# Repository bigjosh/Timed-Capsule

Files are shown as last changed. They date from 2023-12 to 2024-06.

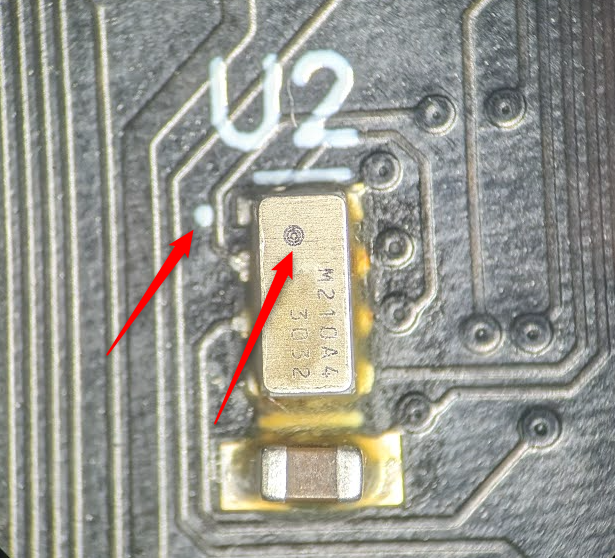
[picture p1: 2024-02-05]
hardware/assembly-package/Orientation U2.png

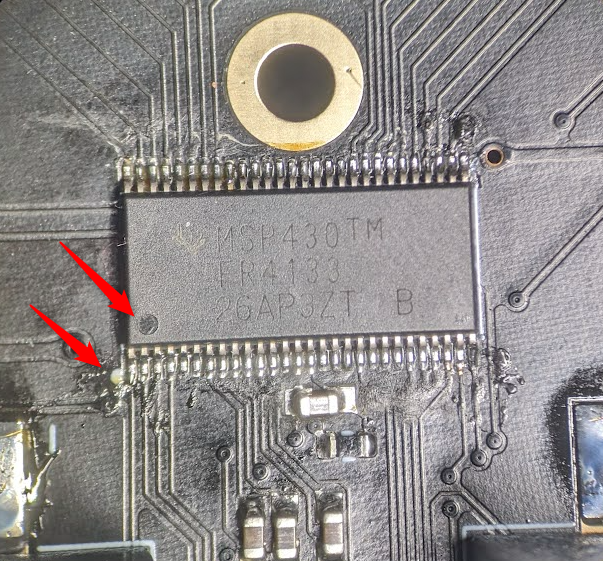
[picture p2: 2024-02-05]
hardware/assembly-package/Orientation U1.png

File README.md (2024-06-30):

# Timed Capsule

PCB and firmware for the CW&T Timed Capsule project.



The Timed Capsule is a commitment device. You put something in the capsule and set the timer for between 1 hour and 100 years and you will not be able to (nondestructively) get the thing for that long. 



## Design goals:

* Run for decades on 2xAA batteries.
* Stay accurate to to within ±2ppm over the lifetime.
* Have enough power at the end of 50 years in storage to still be able to decisively open the locking mechanisim. 
* Replaceable batteries

## Critical parts:

* MSP430FR4133 processor for LCD driving and supervision
* RV3032-C7 RTC for precision timekeeping
* 7-digit, dynamic LCD glass 
* 4x Energizer Ultimate Lithium AA batteries
* Solenoids which pull decicively at 6V
* Optional TPS7A0230 3V regulator for generating LCD bias voltage

## Method of Operation

### Set timer

Use the `MOVE` button to change cursor posision on the LCD, use the `CHANGE` button to change the current position. 

The rightmost position is the units and can be...

| Value | Units | 
| - | - |
| `H` | Hours |
| `d` | Days |
| `y` | Years | 

Note that a [year is 365.2422 days](https://pumas.nasa.gov/sites/default/files/examples/04_21_97_1.pdf). 

### Lock 

1. Turn the locking handle on the top clockwise 1/4 turn until it stops.
2. Release the handle and let it return to the resting position.

### Wait

Durring the countdown, the LCD  will rotate though...

1. Days remaining as 'xxxxxd`.
2. Hours, minutes, and seconds until the current day is done as `HHMMSS`.

... stopping on each screen for 1 second. 

If there is less than 1 day remaing until unlock, then the `HHMMMSS` display will show continuously. 

### Unlock

At the appointed hour, the locking mechanisim will automatically retract with a satisfying thud. You should then be able to remove the cap.

Note that the mechanisim will not be able to release unless the handle is in the resting position (turned all the way counter clockwise). If you accedentially turn the handle clockwise when the mechanisim is unlocking, then it will stay locked.
Since the timer automatically resets to 1 hour after each unlock attempt, you can turn the handle counter clockwise and then clockwise again to restart the countdown and - as long as you let the handle return to the resting position- it will unlock then.

## Interesting twists

### Solenoids

It is hard to find common solenoids that definitively actuate at voltages/currents available with our AA batteries, so we picked the solenoids carefully and use an extra pair AA batteries soley for a voltage boost at the moment we pull them. You might suggest using either a boost inductor-based boost circuit or a capacitor-based charge pump to avoid ths, but it would require some very big parts to store enough energy to be useful here (we can not use electrolitic caps since they will likely fail over the decades). It is hard to compete with the density of chemical energy! You might also suggest using a motor and gears to do the actuation (this is how most battery powered door locks do it), but it is hard to imagine gears that stay reliable after sitting still for 50 years. 

### Oscilator

We are using the MSP430's Very Low Power Oscilator (VLO) to drive the LCD since it is actually lower power than the 32Khz XTAL. It is also slower, so more power savings. The internal VLO also empreically uses less total power than using the RV3032 clkout to drive the MSP430's LCD clock, which is supprising. 

### MSP430 LPMx.5 modes

We do NOT use the MSP430's "LPMx.5" extra low power modes since they end up using more power than the "LPM4" mode that we are using. This is becuase it takes 250us to wake from the "x.5" modes and durring this time, the MCU pulls about 200uA. Since we wake every second, this is just not worth it. If we only woke every, say, 15 seconds then we could likely save ~0.3uA by using the "x.5" modes.

### LCD software optimications

To make LCD updates as power efficient as possible, we precomute the LCDMEM values for every second and minute update and store them in tables. Because we were careful to put all the segments making up both seconds digits into a single word of memory (minutes and hours also), we can do a full update with a single 16 bit write. We further optimize by keeping the pointer to the next table lookup in a register and using the MSP430's post-decrement addressing mode to also increment the pointer for free (zero cycles). This lets us execute a full update on non-rollover seconds in only 4 instructions (not counting ISR overhead). This code is here...
[CCS%20Project/tsl_asm.asm#L91](CCS%20Project/tsl_asm.asm#L91)

We also further reduce power using the MSP430's LCD buffer hardware. We keep the "days" display in one LCD buffer and the "HHMMSS" in the the other buffer. This way we only need to update one bit to switch between the two and therefore only end up needing to write to the "days" page once per day to update the day count. 

Finally, we use the MSP430's blinking segment buffer to create the cursor in setting mode. Since this is all done in hardware, the MCU is always sleeping in setting mode
except immedeately after a button is pushed or the trigger is activated.

### Power supply glitch filter

The 100 ohm resistor between the battery and the Vcc pin of the MCU is needed to create a low pass filter. This slows down the voltage changes when the solenoids turn on and off (these solenoids pull more than 1 amp). The MCU can brown out if it sees a change on the Vcc pin faster than 1V/us. The maximum current the MCU can pull is only about 2mA so we only lose 0.2 volts of power supply voltage worst case, and this chip can run down to 1.8V so this does not cost us any run time.

### Keeping backup countdown in FRAM

This chip has FRAM memory which is consistant across power cycles and resets. We keep the current countdown time left (with 1 minute resoltion) in FRAM so in case the chip ever resets, then we will pick up where we left off. There is some complexity in making sure that updates to this FRAM counter are atomic so it does not get corrupted if we happen to fail in the middle of an update. 

### LCD hardware optimizations

We need regulated 3.0V DC for the LCD bias voltage, but we have 3V-3.6V coming from the batteries. 

The MSP430 has a built in adjustable voltage regulator. Is this more efficient than the very-efficient TPS7A30 dedicate regulators?

Let's test! Here we display the specified pattern and then go into LPM4 sleep and then measure current using a Joulescope. 

Vcc=3.55V<br>(2xAA fresh)
| Pattern | TPS7A30 |  Internal 2.96V  |  Internal 3.08V |
| - | -: | -: | -: |
| blank | 0.85uA | 1.10uA | 1.12uA |
| "111111" | 1.01uA | 1.65uA |  |
| "555555" | 1.31uA | 2.36uA |  |
| "888888" | 1.19uA | 2.05uA | 2.12uA |

Ok, since we will spend most of our lifetime around 3.55V, it is clear that the TPS7A is worth it!

Interesting that the 1uF capacitor on the basis pin can maintain the display for several seconds after disconnected from the regulator. 

Let's just make sure there are no surpises when we least want them - when the battery is reaching the end of its life...

Vcc=2.6V<br>(2xAA after many decades)
| Pattern | TPS7A30 |  Internal 2.96V  |
| - | -: | -: |
| "555555" | 1.03uA |  | 
| "888888" | 1.00uA | 2.02uA | 

Good enough. Note that since the TPS7A is only a regulator and not a carge pump that once the Vcc drops below 3V that the LCD will start to 
get dimmer (actually you will just need to look at it from a lower angle to see the same contrast level). I see this as a feature for this
application since once we get below 3V then I want to user to get some feedback that the batteries are getting low, but for other applications or
if you are using alkaline batteries then you might want to switch to the internal charge pump below 3V. 

And just for fun, let's see how much power we could save if we did not need a regulated voltage soruce at all...

Vcc=3.0V
| Pattern | Direct Vcc |
| - | -: |
| "555555" | 1.25uA | 

... so, wow, the TPS7A is really efficient for generating the LCD bias voltage in this application.

Since we are now going to include the TPS7A in the design, could we get even more power savings by having it also regulate the Vcc for the MSP430?

Vcc=3.55V
| Test | Direct Vcc | TSP7A2030 |
| - | -: |  -: |
| Static "123456" | 1.14uA | 1.14uA |
| 1Hz digit updates | 1.09uA | 1.06uA |

So ever so slight savings. Probably not worth the loss in flexibility since if we only use the TSP7A20 for the LCD bias voltage and we ever can not get the part, we can 
just omit it from the board and and instead enable the internal regulator.

## Build notes

### Current Usage

| Mode | Vcc=3.55V<br>(2xAA fresh) | Vcc=2.6V<br>(2xAA after many decades) |  Vcc=7.0V<br>(4xAA fresh) | Vcc=5.2V (4xAA after many decades) |
| - | -: | -: | -: | -: |
| Setting mode | 1.3uA | 1.2uA |  |  |
| Countdown mode | 1.1uA | 1.0uA |  |  |
| Unlock |  |  | 1.2A | 1A |

3.55V is approximately the voltage of a pair of fresh Energizer Ultra batteries.
2.6V is approximately the voltage when the screen starts to become hard to read. 

Note that voltage drop over time is not expected to be linear with Energizer Ultra cells. These batteries are predicted to spend most of their lives towards the higher end of the voltage range and only start dropping when they get near to their end of life.  

### Measurement conditions

Production board from initial batch. Bare PCB on my desk (not in tube).  
68F
80%RH

(Higher humidity and temperature tends to increase current consumption. Need some different weather conditions to quantify this!)

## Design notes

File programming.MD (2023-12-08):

1. Download and install Code Cmposer Studio (CCS)...
   https://www.ti.com/tool/CCSTUDIO
2. Clone the TSL-calibre-MSP repo...
   https://github.com/bigjosh/TSL-calibre-MSP/
3. Open the TSL project in CCS using "Project->Import existing CCS/Eclipse Project" and picking the "CCS Project" folder in the repo. 
5. Select "Project->Build Configurations->Set Active->Release" from the CCS menu.
5. Select "Project->Build Project" from the CCS menu and make sure there are no errors. Note that this takes longer than you think it should and the only indication that it is working is in the lower right corner of the CCS window.   
6. Plug the EZ-FET programming board into a USB port. 
7. Connect the wires from the EZ-FET  to the TSP board like...
   |  EZ-FET | TSL |
   | -  | - |
   | Ground | G | 
   | SBWTCK | T | 
   | SBWTDIO | R |
8. Either put batteries into the TSL or connect the TSL `V` pin to the `3V3` pin on the EZ-FET.  
9. Pick "Run->Load->Pick program to load in the CCS menu.
10. Push the "Browse Project" button and pick "Release/TSL-caible-MSP.out" and click OK. 
11. Wait for the program to download. This also takes longer than you think and does not have good feedback.
12. After all the popups go away, the TSL should be running the newly downloaded firmware.

For now on, you can also just pick "Run->Load->TSL-calibre-MSP.out" to compile and download the program again.

If you used the EZ-FET 3V3 pin for power, then you can now test the power usage by clicking on the Energy Trace icon () and 
then clicking on the play button in the new energy trace window. Remember that (1) the trigger switch uses a lot of power until the pin is initially put in (switch opened), and (2) 
there is a lot more software optimization to be done.

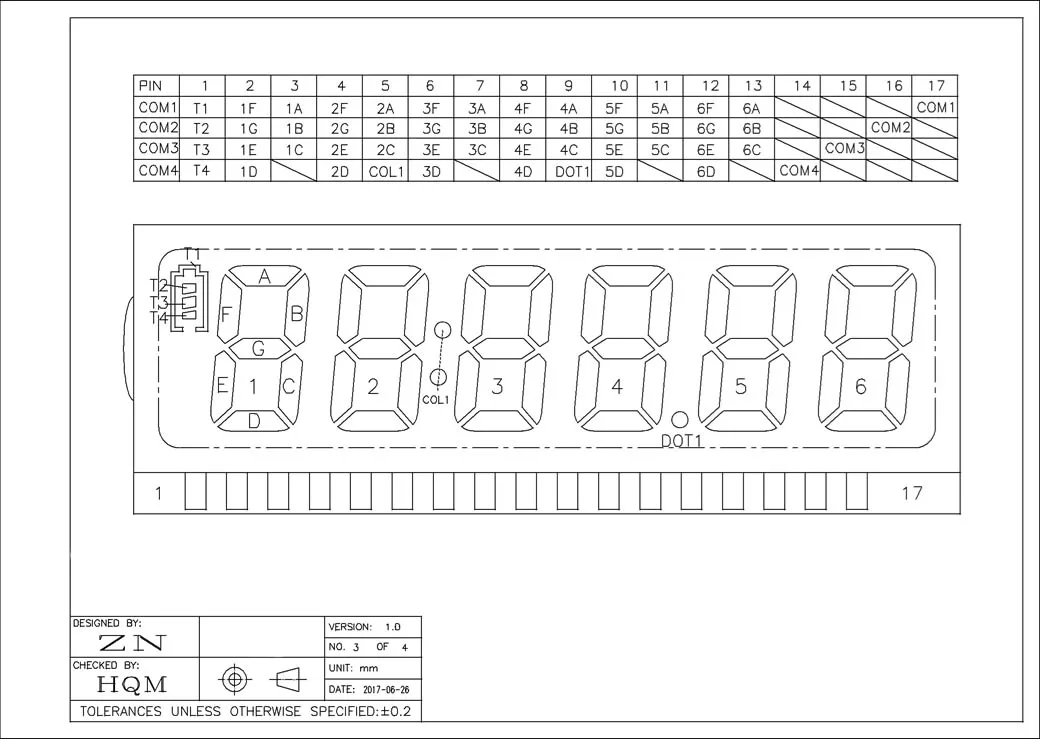
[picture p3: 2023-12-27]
docs/LCD 6-digit pinout.webp

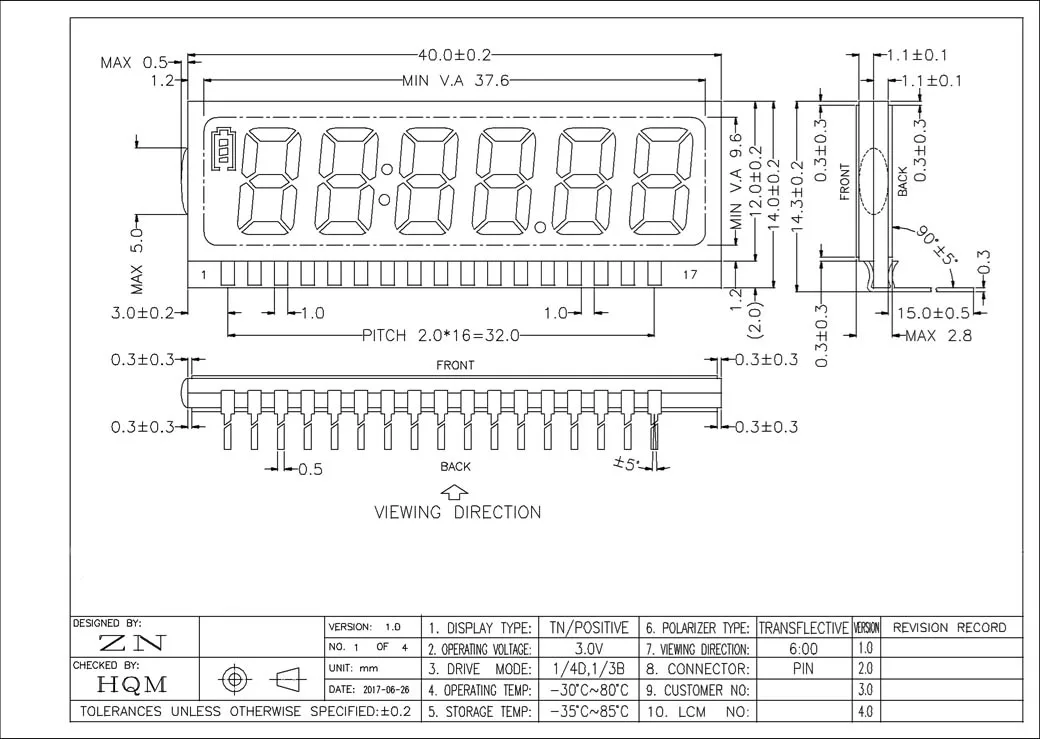
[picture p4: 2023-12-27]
docs/LCD 6-digit drawing.webp

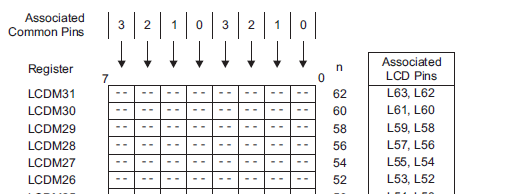
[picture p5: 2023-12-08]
MSP430 LCD memory map.png

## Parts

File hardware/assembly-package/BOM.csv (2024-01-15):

RefDes | Name | Value | Manufacturer | Place | Subsitution | Budget Price at 1K units | URL
C1 | CAP_0603 | CAP CER 1UF 16V X7R 0603 | Murata |  | Possible | 0.02 | https://www.digikey.com/en/products/detail/taiyo-yuden/EMK107C6105KA-T/6563455
C3 | CAP_0603 | CAP CER 1UF 16V X7R 0603 | Murata |  | Possible | 0.02 | https://www.digikey.com/en/products/detail/taiyo-yuden/EMK107C6105KA-T/6563455
C4 | CAP_0603 | CAP CER 1UF 16V X7R 0603 | Murata |  | Possible | 0.02 | https://www.digikey.com/en/products/detail/taiyo-yuden/EMK107C6105KA-T/6563455
C5 | CAP_0603 | CAP CER 1UF 16V X7R 0603 | Murata |  | Possible | 0.02 | https://www.digikey.com/en/products/detail/taiyo-yuden/EMK107C6105KA-T/6563455
C7 | CAP_0603 | CAP CER 1UF 16V X7R 0603 | Murata |  | Possible | 0.02 | https://www.digikey.com/en/products/detail/taiyo-yuden/EMK107C6105KA-T/6563455
C8 | CAP_0603 | CAP CER 1UF 16V X7R 0603 | Murata |  | Possible | 0.02 | https://www.digikey.com/en/products/detail/taiyo-yuden/EMK107C6105KA-T/6563455
C2 | CAP_0805 | CAP CER 47UF 6.3V X5R 0805 | Murata |  | Possible | 0.07 | https://www.digikey.com/en/products/detail/CL21A476MQYNNNG/1276-6467-1-ND/5958095
C6 | CAP_0805 | CAP CER 47UF 6.3V X5R 0805 | Murata | DNP | Possible | 0
C9 | CAP_0805 | CAP CER 47UF 6.3V X5R 0805 | Murata | DNP | Possible | 0
J1 | LCD | 30PIN TN Positive 12 Digit 7 Segment |  | DNP |  | 1 | na
J3 | Programming pads | PDI-6 |  | DNP
L1 | Flash LED | 62-227ET/KK7D | Everlight High Power LEDs |  | Possible | 0.16 | https://www.digikey.com/en/products/detail/everlight-electronics-co-ltd/62-227ET-KK7D-3M5050X6Y62629U6-2T-EU/7930856
L2 | Flash LED | 62-227ET/KK7D | Everlight High Power LEDs |  | Possible | 0.16 | https://www.digikey.com/en/products/detail/everlight-electronics-co-ltd/62-227ET-KK7D-3M5050X6Y62629U6-2T-EU/7930856
Q1 | MOSFET Transistor | 2N7002K | NXP-Philips |  | Possible | 0.05 | https://www.digikey.com/en/products/detail/rohm-semiconductor/RK7002BMT116/4924083
Q2 | MOSFET Transistor | 2N7002K | NXP-Philips |  | Possible | 0.05 | https://www.digikey.com/en/products/detail/rohm-semiconductor/RK7002BMT116/4924083
S1 | Trigger Switch | ESE18R61D | Panasonic |  |  | 0.63 | https://www.digikey.com/product-detail/en/panasonic-electronic-components/ESE-18R61D/P13373SCT-ND/822309
U1 | MCU | MSP430FR4133IG56 | TI |  |  | 1.15 | https://www.digikey.com/en/products/detail/texas-instruments/MSP430FR4133IG56/5067017
U2 | RTC | RV-3032-C7 | Micro Crystal |  |  | 2.95 | https://www.digikey.com/en/products/detail/micro-crystal-ag/rv-3032-c7-32-768khz-2-5ppm-ta-qa/16273065
U3 | REGULATOR | TPS7A0230PDBVR | TI |  | Possible | 0.5 | https://www.digikey.com/en/products/detail/texas-instruments/TPS7A0230PDBVR/12165118
U4 | Battery Holder | KEYSTONE1024 | Keystone |  |  | 1.601 | https://www.digikey.com/product-detail/en/keystone-electronics/1024/36-1024-ND/2178268
U5 | Battery Holder | KEYSTONE1024 | KeyStone |  |  | 1.601 | https://www.digikey.com/product-detail/en/keystone-electronics/1024/36-1024-ND/2178268
T1 | Test pads | CAP_0603 |  | DNP
R7 | RES_0603 | RES 100 OHM
-
S1 | Reed Switch | ESE18R61D | TS04-66-43-BK-160-SMT |  |  | 0.18 | https://www.digikey.com/en/products/detail/cui-devices/TS04-66-43-BK-160-SMT/15634332
S2 | Button | ESE18R61D | TS04-66-43-BK-160-SMT |  |  | 0.18 | https://www.digikey.com/en/products/detail/cui-devices/TS04-66-43-BK-160-SMT/15634332
S3 | Button | ESE18R61D | TS04-66-43-BK-160-SMT |  |  | 0.18 | https://www.digikey.com/en/products/detail/cui-devices/TS04-66-43-BK-160-SMT/15634332
B1 | Battery Holder | KEYSTONE1089 | Keystone |  |  | 2.7 | https://www.digikey.com/en/products/detail/keystone-electronics/1089/5118851
B2 | Battery Holder | KEYSTONE1089 | Keystone |  |  | 2.7 | https://www.digikey.com/en/products/detail/keystone-electronics/1089/5118851
Q1 | MOSFET Transistor | A03422 | Alpha & Omega Semiconductor Inc. |  | Possible | 0.11 | https://www.digikey.com/en/products/detail/alpha-omega-semiconductor-inc/AO3422/1855787

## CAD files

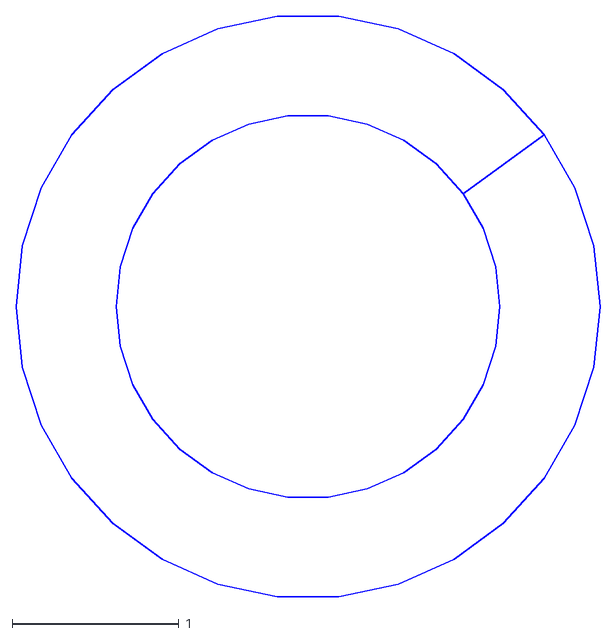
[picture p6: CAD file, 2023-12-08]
hardware/diptrace/mounting hole anulus shape phase2.dxf
3.50 x 3.48

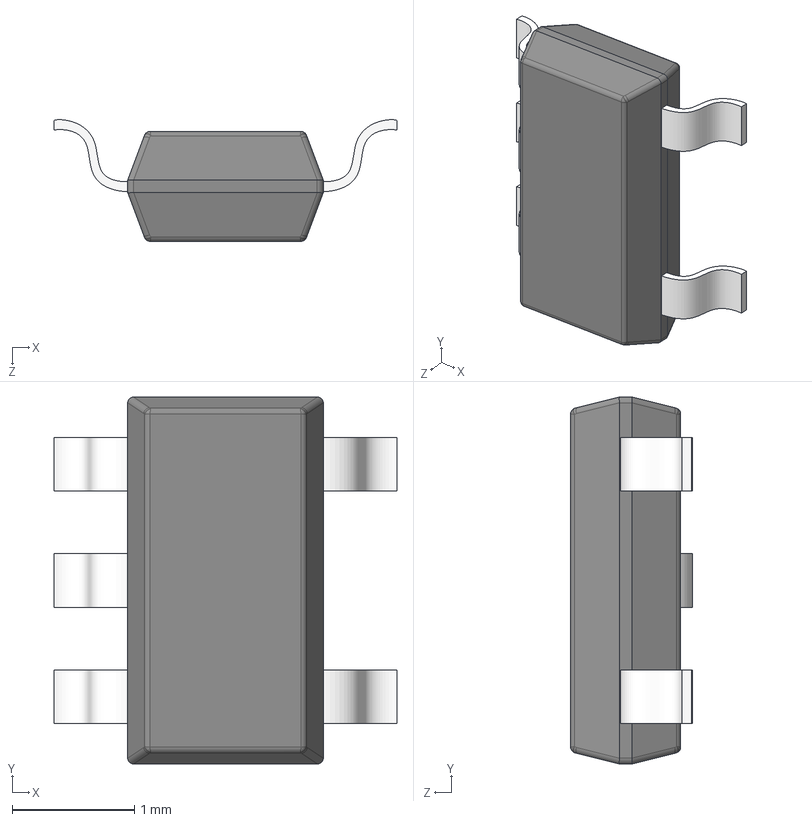
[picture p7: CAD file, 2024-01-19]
hardware/diptrace/3d/sot23-5.step
2.80 x 3.00 x 0.995 mm
sot23-5
sot23-5_001

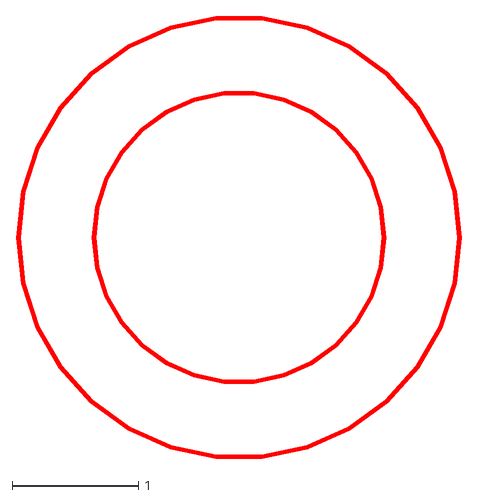
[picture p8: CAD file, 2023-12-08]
hardware/diptrace/mounting hole anulus shape phase1.dxf
3.53 x 3.51

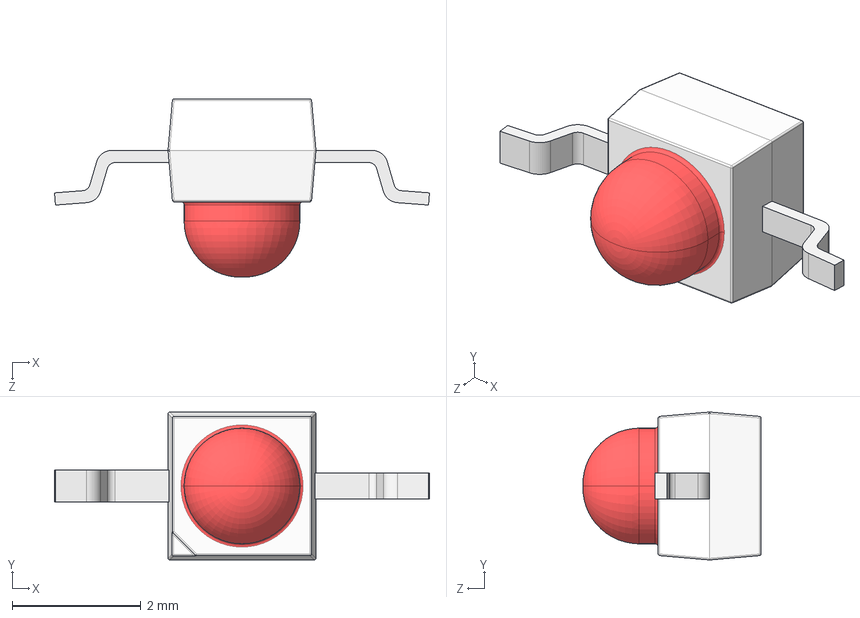
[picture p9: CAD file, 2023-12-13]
hardware/diptrace/3d/VLDR1235R.stp
5.83 x 2.30 x 2.77 mm

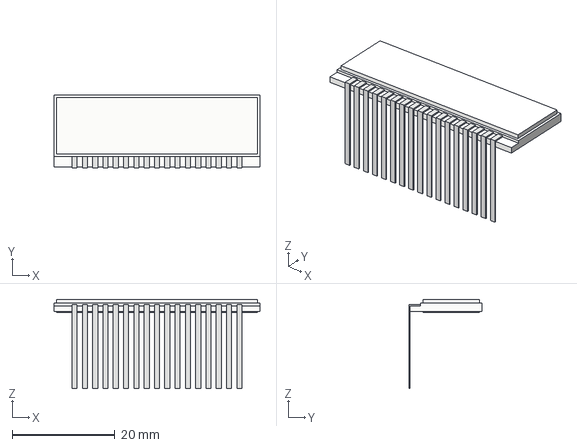
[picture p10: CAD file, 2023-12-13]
hardware/diptrace/3d/6 DIGIT LCD v2.step
40.0 x 14.2 x 17.4 mm

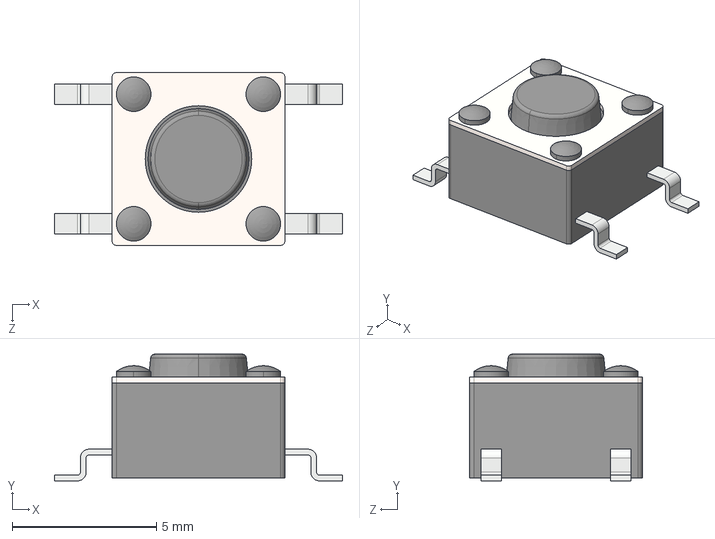
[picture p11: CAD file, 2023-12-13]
hardware/diptrace/3d/TS04-66-43-BK-160-SMT.stp
10.0 x 4.40 x 6.00 mm

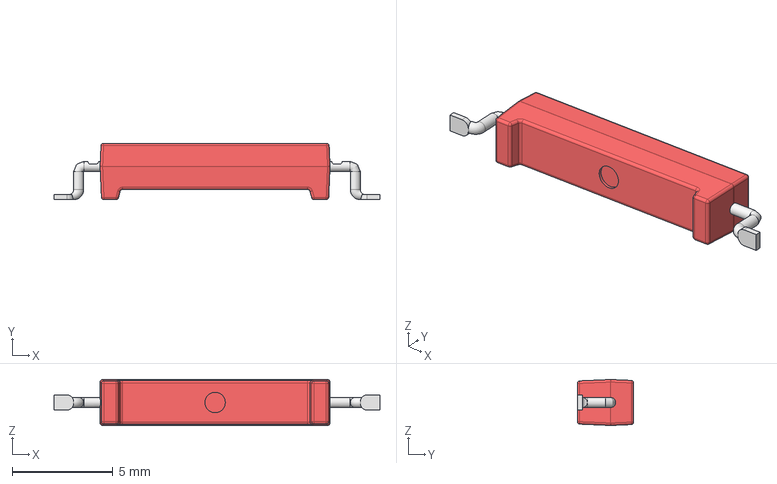
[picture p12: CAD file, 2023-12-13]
hardware/diptrace/3d/CT10-XXXX-G1-A.stp
16.2 x 2.81 x 2.29 mm
CT10- SERIES
CT10-G1

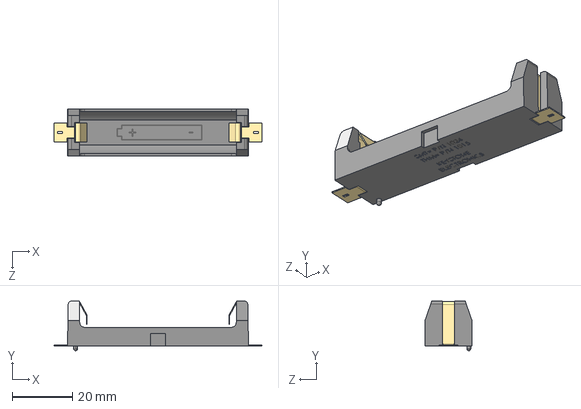
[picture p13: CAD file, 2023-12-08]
hardware/diptrace/3d/keystone-PN1024.STEP
68.9 x 16.4 x 15.5 mm

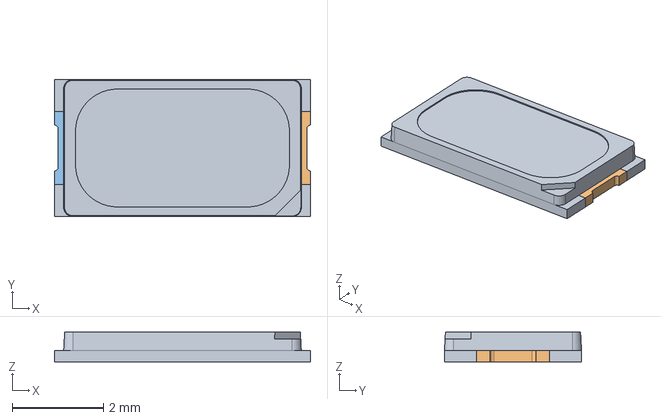
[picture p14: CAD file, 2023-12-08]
hardware/diptrace/3d/62-217D.STEP
5.60 x 3.00 x 0.65 mm
62-127D-1

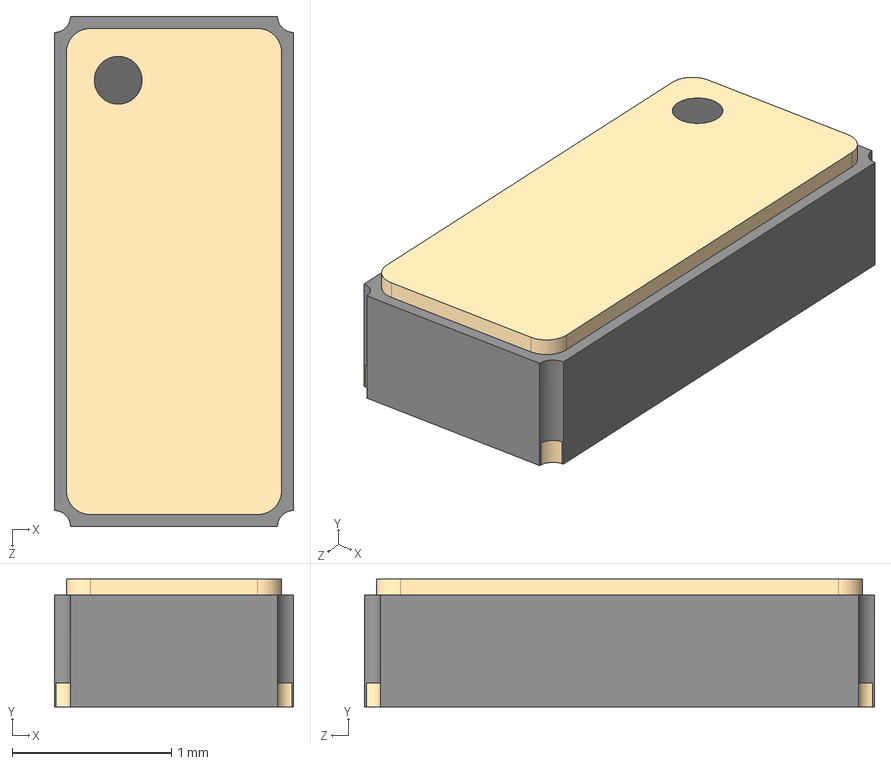
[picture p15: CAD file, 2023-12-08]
hardware/diptrace/3d/RV-3032-C7-32.768KHZ-3PPM-TA-QA.STEP
1.50 x 0.8 x 3.20 mm

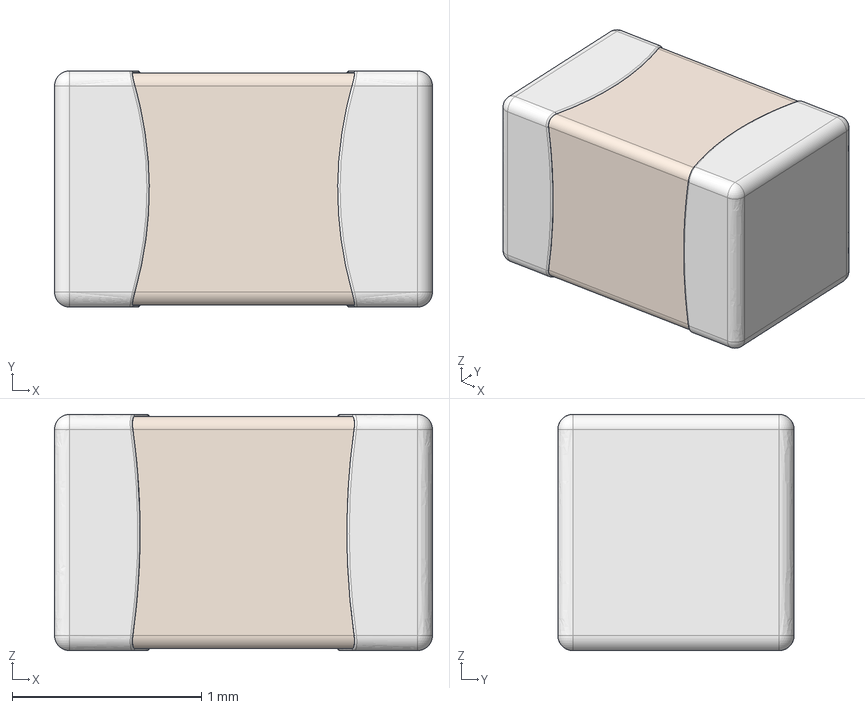
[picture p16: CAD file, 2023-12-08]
hardware/diptrace/3d/Ceramic_Capacitor_0805_h50mil.step
2.00 x 1.25 x 1.25 mm
Pin1
Pin2
CeramicBody

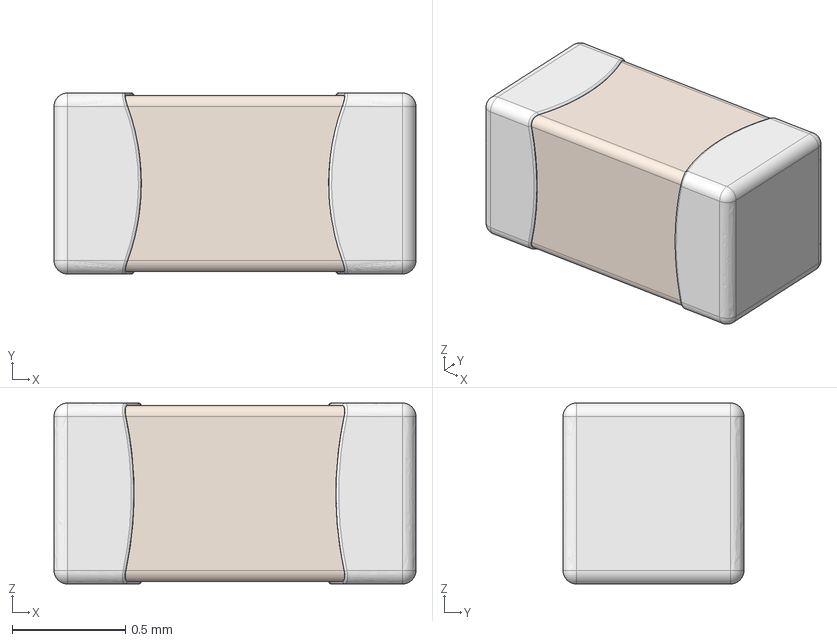
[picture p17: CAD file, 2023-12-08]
hardware/diptrace/3d/Ceramic_Capacitor_0603.step
1.60 x 0.8 x 0.8 mm
Pin1
Pin2
CeramicBody

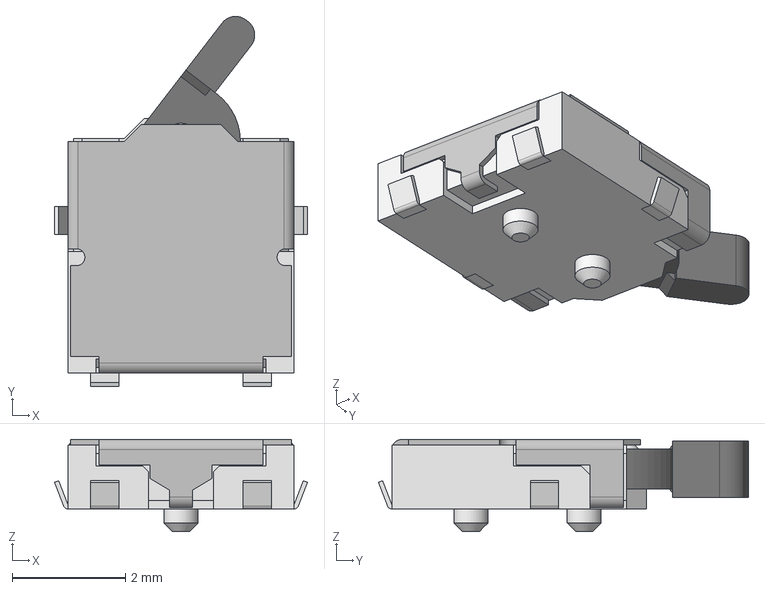
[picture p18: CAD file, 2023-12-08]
hardware/diptrace/3d/ESE18R61B.step
4.47 x 6.54 x 1.63 mm

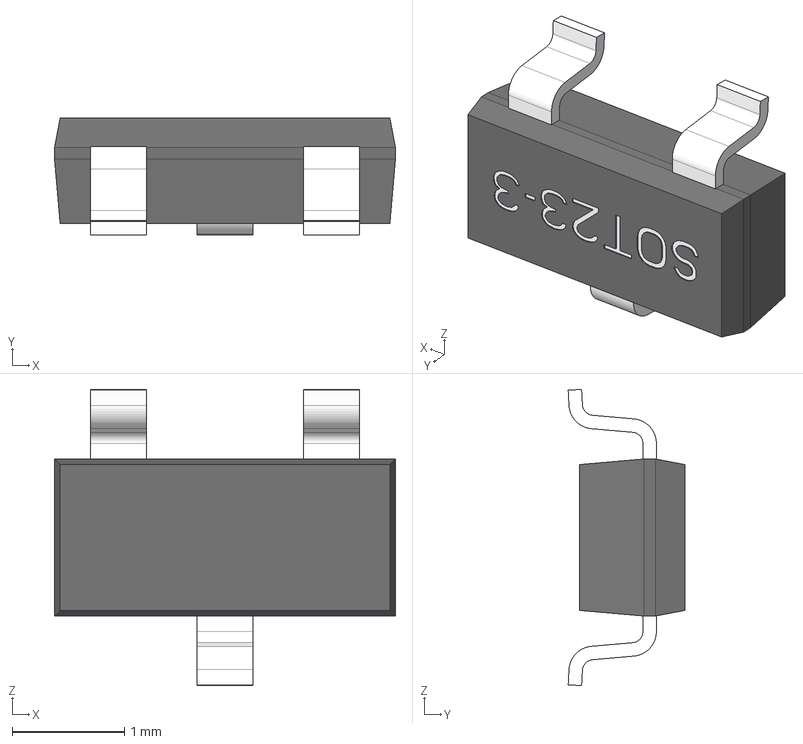
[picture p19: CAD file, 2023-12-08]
hardware/diptrace/3d/sot23-3_p0-95_l3-04_w1-4.stp
3.04 x 1.04 x 2.64 mm

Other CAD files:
hardware/diptrace/3d/SOT95P280X145-5N.step
hardware/diptrace/3d/393570002.stp
hardware/diptrace/3d/82548PLCC-2_package_3D.stp

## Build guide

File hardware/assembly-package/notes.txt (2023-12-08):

1.
No ultrasound cleaning - RTC clock part U2 is sensitive to vibration.

2.
LCD parts are to be hand soldered. The LCD face on the TOP side of the PCB. LCD 
must have clearance above parts below. Use a jig or shim to maintain uniform 1.6mm 
clearance between LCD bottom and PCB top while solderning. Soldering to be done from
the BOTTOM side of PCB. 

3.
LCD part is heat sensitive. Avoid overheating when soldering. Solder alternating
pins to avoid over heating LCD. 

4.
Use the solder reflow profile for RTC clock part U2, included in this directory. 

5.
Parts U1, U2, L1, & L2 are orienation sensitive. See photos in this directory for proper
rotation.

6.
PCB Parameters
Layer:2 Layers
Material:FR-4
Thickness:1.6 mm
Solder Mask:Matt black
Silkscreen:White (Silk layer may be omitted)
Surface Finish:Immersion gold(ENIG) (1U")

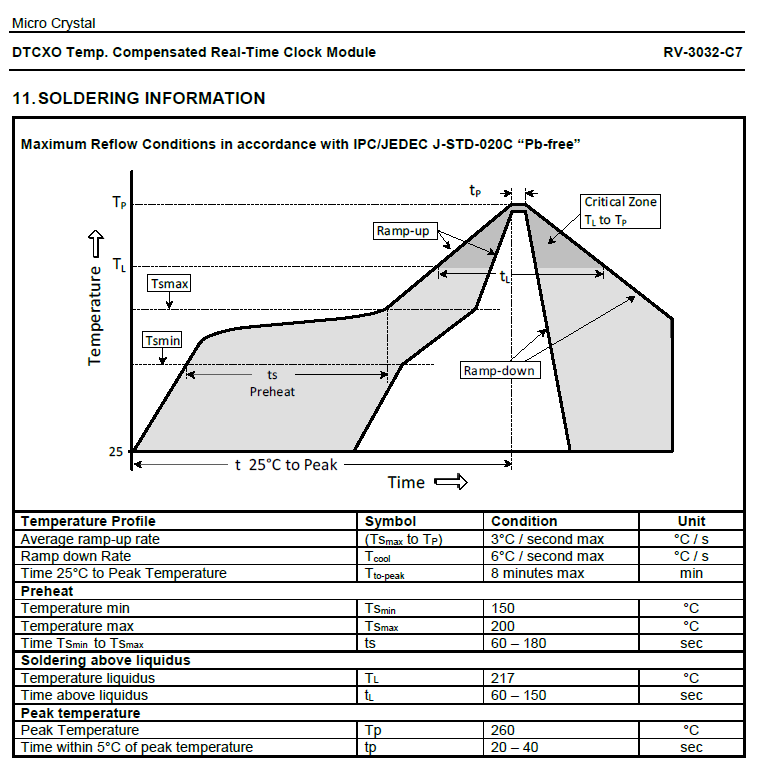
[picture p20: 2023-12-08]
hardware/assembly-package/RV3032-C7 reflow profile.png

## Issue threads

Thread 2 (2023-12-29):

Order the correct SMD battery holders

bigjosh, 2023-12-29:

bigjosh, 2024-01-16:
Ordered from digikey

Closed 2024-01-16.

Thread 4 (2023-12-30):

How to make board-to-solenoid connections?

bigjosh, 2023-12-30:
No matter what, current pads are too small. Make them bigger? Or go for a connector or terminal blocks?

bigjosh, 2024-01-16:
Probably the most robust is just the current solder pads, but this requires pre- cutting, stripping, tinning the wires, and then assembly is a bit fiddly getting all the wires thought he holes, and then you have to solder them. Also means you have to desolder to take everything apart. :/

To avoid needing to thread the wires though the holes, we could instead make notched in the board edge for the wires. Ugly?

Could use screw terminal blocks to avoid the need to solder during assembly. Here are some ok ones that are at least black...
https://www.digikey.com/en/products/detail/te-connectivity-amp-connectors/2383942-2/14639235
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

We could use the connectors that match the existing plugs that come on the wires...
https://www.digikey.com/en/products/detail/jst-sales-america-inc/S2B-PH-SM4-TB/926655
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
....but slightly ugly and still have to deal with threading the wires though the holes during assembly and also must deal with all the extra wire so that will likely need to be coiled up and zip-tied, but that is ugly and should be secured to not move around and cause problems? Also do we trust those connectors to never accidentally come out?

bigjosh, 2024-01-20:
Going with terminal blocks for now as per CW. I picked thru-hole because I don't like that the only thing holding the SMD ones on is the copper adhesive. Maybe if production ramps up then we will switch to SMD or a better solution.

Closed 2024-01-20.

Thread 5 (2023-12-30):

Pick a flyback suppressor

bigjosh, 2023-12-30:
LEDs are pretty, but schottkey would maybe keep the solenoid open slightly longer? Or maybe a P-Chan MOSFET would keep it open even longer?

bigjosh, 2024-01-16:
White LED looks pretty, but a proper schottkey lets us lower the duty cycle to hold the solenoid by 10% so we should pick function over form.

Closed 2024-01-16.

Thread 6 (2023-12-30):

Move RV3032 CLKOUT to a dedicated interrupt?

bigjosh, 2023-12-30:
Maybe have all the switches share one interrupt so we can hyper optimize the clock interrupt since that is the one that really matters.

bigjosh, 2024-01-16:
Closed with 0b13d7c352ee18a353cbdee77e4bf6a3ce344d33.

Closed 2024-01-16.

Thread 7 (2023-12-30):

Add backdoor?

bigjosh, 2023-12-30:
Should we put in a secret emergency backdoor? Could be something like a knock pattern on the lock switch. The actual pattern could be held as a secret on the programming machine so it does not leak in the source code.

Pragmatic, but is this moral abomination?

bigjosh, 2024-02-05:
NO BACKDOOR - CWT&T
Issue closed with prejudice.

Closed 2024-02-05.

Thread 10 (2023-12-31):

Test again what putting the TPS7A in front of the MCU does for power.

bigjosh, 2023-12-31:
Would clean up the voltage when the solenoids pull, and TI suggests it could save power?

bigjosh, 2024-01-16:
Vcc=3.55V
| Test | Direct Vcc | TSP7A2030 |
| - | -: | -: |
| Static "123456" | 1.14uA | 1.14uA |
| 1Hz digit updates | 1.09uA | 1.06uA |

So ever so slight saving. Probably not worth the loss in flexibility since ifonly use the TSP7A20 for the LCD bias voltage and we can not get it, we can just omit it from the board and and instead enable the internal regulator.

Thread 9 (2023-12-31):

I do not like solenoids

bigjosh, 2023-12-31:
I am scared they are going to bind when the big moment comes.

Maybe go back to the original little ones so we can pull them all simultaneously? Then the interaction could be to have the user turn the locking ring again to unlock, which would lift the sliders off the solenoid shafts so they could move freely?

Or maybe just stick with current solenoids but dither them we open them one at a time but keep each one open until they are all open?

Or maybe have the user turn the ring, then hit each solenoid once with full strength to unsick it, then go back around and open them again but this time holding them open?

bigjosh, 2024-01-16:
We should at least add some teflon inserts where the solenoid shaft touches the latch edge.

bigjosh, 2024-01-16:
Test muscle wires someday.

bigjosh, 2024-02-11:
Maybe wax motors?

https://waxmotor.com/blogs/introduction-to-wax-motor

cheewee2000, 2024-02-14:
Super cool! I like how they work. But wouldn’t it be too easy to hack? Would you be able to put the whole TC into an oven and heat it up to unlock it?

bigjosh, 2024-02-14:
I think we could secure this by having counter acting actuators (CAAs?) that go in the opposite direction but are unpowered.  Super duper simplified sketch...

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

Let's say you heat this whole thing up. Then both A and B will actuate and cancel each other out. To get movement of the linkage, you have to, say, heat only one of the two actuators - which you would do electrically. If you heat only A then the linkage moves to the right, only B and it moves to the left.

Make sense? I think it is secure as long as there is no way to selectively heat one or the other, which would be hard inside a thick metal shell.

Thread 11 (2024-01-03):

Turning Solenoid S1 off and then on again quickly (1ms) resets MCU.  Does not happen with Solenoid S2.

bigjosh, 2024-01-03:
Replacing flyback with schottkey does not fix it.

Connecting reset pin to Vcc with jumper wired does not fix it.

Maybe try replacing S1 with a resistor to see if this is related to inductive load?

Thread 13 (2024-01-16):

How to deal with those wires coming form the solenoids?

bigjosh, 2024-01-16:

bigjosh, 2024-01-16:
Probably the most robust is just the current solder pads, but this requires pre- cutting, stripping, tinning the wires, and then assembly is a bit fiddly getting all the wires thought he holes, and then you have to solder them. Also means you have to desolder to take everything apart. :/

To avoid needing to thread the wires though the holes, we could instead make notched in the board edge for the wires. Ugly?

Could use screw terminal blocks to avoid the need to solder during assembly. Here are some ok ones that are at least black...
https://www.digikey.com/en/products/detail/te-connectivity-amp-connectors/2383942-2/14639235
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

We could use the connectors that match the existing plugs that come on the wires...
https://www.digikey.com/en/products/detail/jst-sales-america-inc/S2B-PH-SM4-TB/926655
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
....but slightly ugly and still have to deal with threading the wires though the holes during assembly and also must deal with all the extra wire so that will likely need to be coiled up and zip-tied, but that is ugly and should be secured to not move around and cause problems? Also do we trust those connectors to never accidentally come out?

bigjosh, 2024-01-16:
Merged with #4

Closed 2024-01-16.

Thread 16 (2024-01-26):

Figure out a way to prove the RTC and its interrupt before locking

bigjosh, 2024-01-26:
There is a failure mode where for some reason the RTC is not ticking or the ticks are not getting to the MCU. IN the case, if the user locks the lock then it will just be stuck at the start time and never count down and never open.

It would be nice to detect this fault and let the user know before they lock up.

We could set a watchdog that is longer than 1 second, and then reset it on every tick interrupt. If the watchdog ever fires, then we display an error message. This is kinda good, but turning the watchdog on uses extra power.

Alternately, we could make the tick ISR do something visually on the LCD every second while in set mode. If the user does NOT see this happening then they could tell something was wrong. Maybe blink the decimal point or something? But how do we communicate to the user that they need to see it flashing?

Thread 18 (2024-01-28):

Rotate solenoid terminal blocks and pass-thru holes to better line up with wire exit locations

bigjosh, 2024-01-28:

cheewee2000, 2024-02-06:
updated the board outline to have slots for wires
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

bigjosh, 2024-02-06:
Added notches as provided, but keeping this issue open die to the fact that these new notches are UGLY. :)
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

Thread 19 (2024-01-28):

LCD height probably too low?

bigjosh, 2024-01-28:
This is only in the fusion model, does not affect PCB.

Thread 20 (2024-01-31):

All those MLCCs ended up right in the flex plane of the PCB thanks to the heavy batteries :/

bigjosh, 2024-01-31:
But where else can they go? The must be very near to those pins on the MCU.
How can we mitigate the flex there?

bigjosh, 2024-02-06:
Thicker PCB? Easy, but more expensive. How thick?

PCBWAY for 5x:

| Thickess |  Cost | Lead |
| - | - | - |
| 1.6mm  | $45.45 | 24h |
| 2.0mm |  $86.44 | 4d |
| 2.4mm | $89.50 | 4d |
| 2.6mm | $171.93 | 8d |

...so big step after 2.4mm so maybe that's the right place to start?

There are no parts on the backside of the PCB so we could also make our own lamination with 2x1.6mm PCBs. Ugly? Also potentially complicates access to the programming pads.

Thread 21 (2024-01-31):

Should the days number be zero or space padded on the left?

bigjosh, 2024-01-31:
Spaces are ever so slightly more power efficient, but zeros show that the full display is working and that you are not missing any digits.

But really a matter of taste.

bigjosh, 2024-01-31:
Currently spaces

bigjosh, 2024-02-03:
Dupe of #15

Closed 2024-02-03.

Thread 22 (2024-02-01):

Should pulling the batteries do a reset and also open the lock?

bigjosh, 2024-02-01:
PRO:
You are setting the time count with the lid off the canister and you somehow mess up and accidentally lock it. Since it is not on the canister, no problem - you can just pull the battery and try again.

CON:
Opens an attack vector if the attacker can somehow make the chip BOD or reset or fuzz or power down inside the locked canister. :/

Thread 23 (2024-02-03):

Solenoid-to-flange screws too long!

bigjosh, 2024-02-03:
Long screws pierce the coil insulation and create a partial short between the frame and each of the two solenoid leads because the screw is hitting the coil right in the middle. So frickin hard to figure out because the problem only shows up when the PCB is screwed into the lid, and then it blows the MOSFET!
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

bigjosh, 2024-02-03:
M2x4 is too long.

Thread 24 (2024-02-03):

Trigger magnet is too weak

bigjosh, 2024-02-03:
Need a bigger mangent.

cheewee2000, 2024-02-06:
I put a bigger magnet in. It works, but if I spin the lever quickly, into the lock position, it doesn't trigger the switch. It seems to only trigger when I pass over the reed switch slowly.

bigjosh, 2024-02-06:
Maybe even stronger magnet? Or two weak magnets? Or a thin magnet that sits in the gap between the lever and the PCB (is there room in here?

This turns out to not be *critical* because the user can always turn the lever again until the trigger registers, but would be bad UI to have it not register under normal conditions.

cheewee2000, 2024-02-08:
It seems like the perfectly aligned magnet doesn't trigger the reed switch. So I tried moving the reed switch slightly off axis. and this seems to work reliably.

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

bigjosh, 2024-02-14:
That is so brutal. Hopefully in future units we can move/rotate the magnet rather than the switch? As per #14.

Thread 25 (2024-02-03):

Test  BSS806NEH6327XTSA1 MOSFET

bigjosh, 2024-02-03:
SHould be drop-in replacement, but slightly lower Rds so higher solenoid coil current.

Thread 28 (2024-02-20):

Make batteries changeable from outside the locked compartment

bigjosh, 2024-02-20:
Solves so many problems. If batteries go dead during the countdown, just change them. Fail safe.

Does require making sure that the counter is persistent across power cycles, but the support for this is already in place.

Does require making sure that the battery compartment does not create any new physical attack vector. Maybe machine a pocket for it in the top of the lid and only tiny protected hole for wires? Or integrate the battery contacts into the sides of the pocket with an insulator to isolate them from the lid metal?

The power lines now must also have attack prevention so at least a zeener for over voltage and a self reset fuse? Maybe inductor for current fuzz resistance?

cheewee2000, 2024-03-29:
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
how about something like this? two pins that you an alligator clip to (or press a 9v battery against) to power it?

or what about using these battery holders? https://www.digikey.com/en/products/detail/bulgin/BX0011-1/1980754 so the battery goes in vertically from the front plate.

bigjosh, 2024-03-29:
I had imagined just normal AA battery bays, except that are accessible from the top. And they are metal and secure. I think it would be obvious to the user how/when to use these. Is there room? I think once we switch to something like muscle wire or wax motors then we can get by with only 2xAA.

>how about something like this? two pins that you an alligator clip to (or press a 9v battery against) to power it?

That is a solution for the case where the batteries are strong enough to keep the counter going but not strong enough to open the latches, and I think it does accomplish this. But I was hoping for a more general solution where you can change the actual batteries that power both functions. Just seems cleaner to me? With this solution, I do not think it will be hard to make it clear what case those are for and when to use them to a user 100 years from now without adding several sentences of text somewhere.

>or what about using these battery holders?

Those are cool! Can you make them secure? Maybe put metal all around them on the inside? Is there room for all that? Maybe easier to make your own version of these out of all metal?

cheewee2000, 2024-03-29:
There's barely enough room to fit the two vertical battery holders. But I'll try! How would muscle wire or wax motors defend themselves from a heat attack?

cheewee2000, 2024-03-29:
If we make our own AA holder, could we make the top plate (and the whole scuba tank) ground? So the battery cap could just be a piece of aluminum that connects to the minus side of the battery?

bigjosh, 2024-03-30:
I think so! The only issue would be making sure that there was no way to hurt the PCB by sending signals on the externally accessible housing. I can not think of how this could be a problem, but we should ask other people if they can!

bigjosh, 2024-03-30:
How to defend against attacks on thermal actuators...
https://github.com/bigjosh/Timed-Capsule/issues/9#issuecomment-1944093638

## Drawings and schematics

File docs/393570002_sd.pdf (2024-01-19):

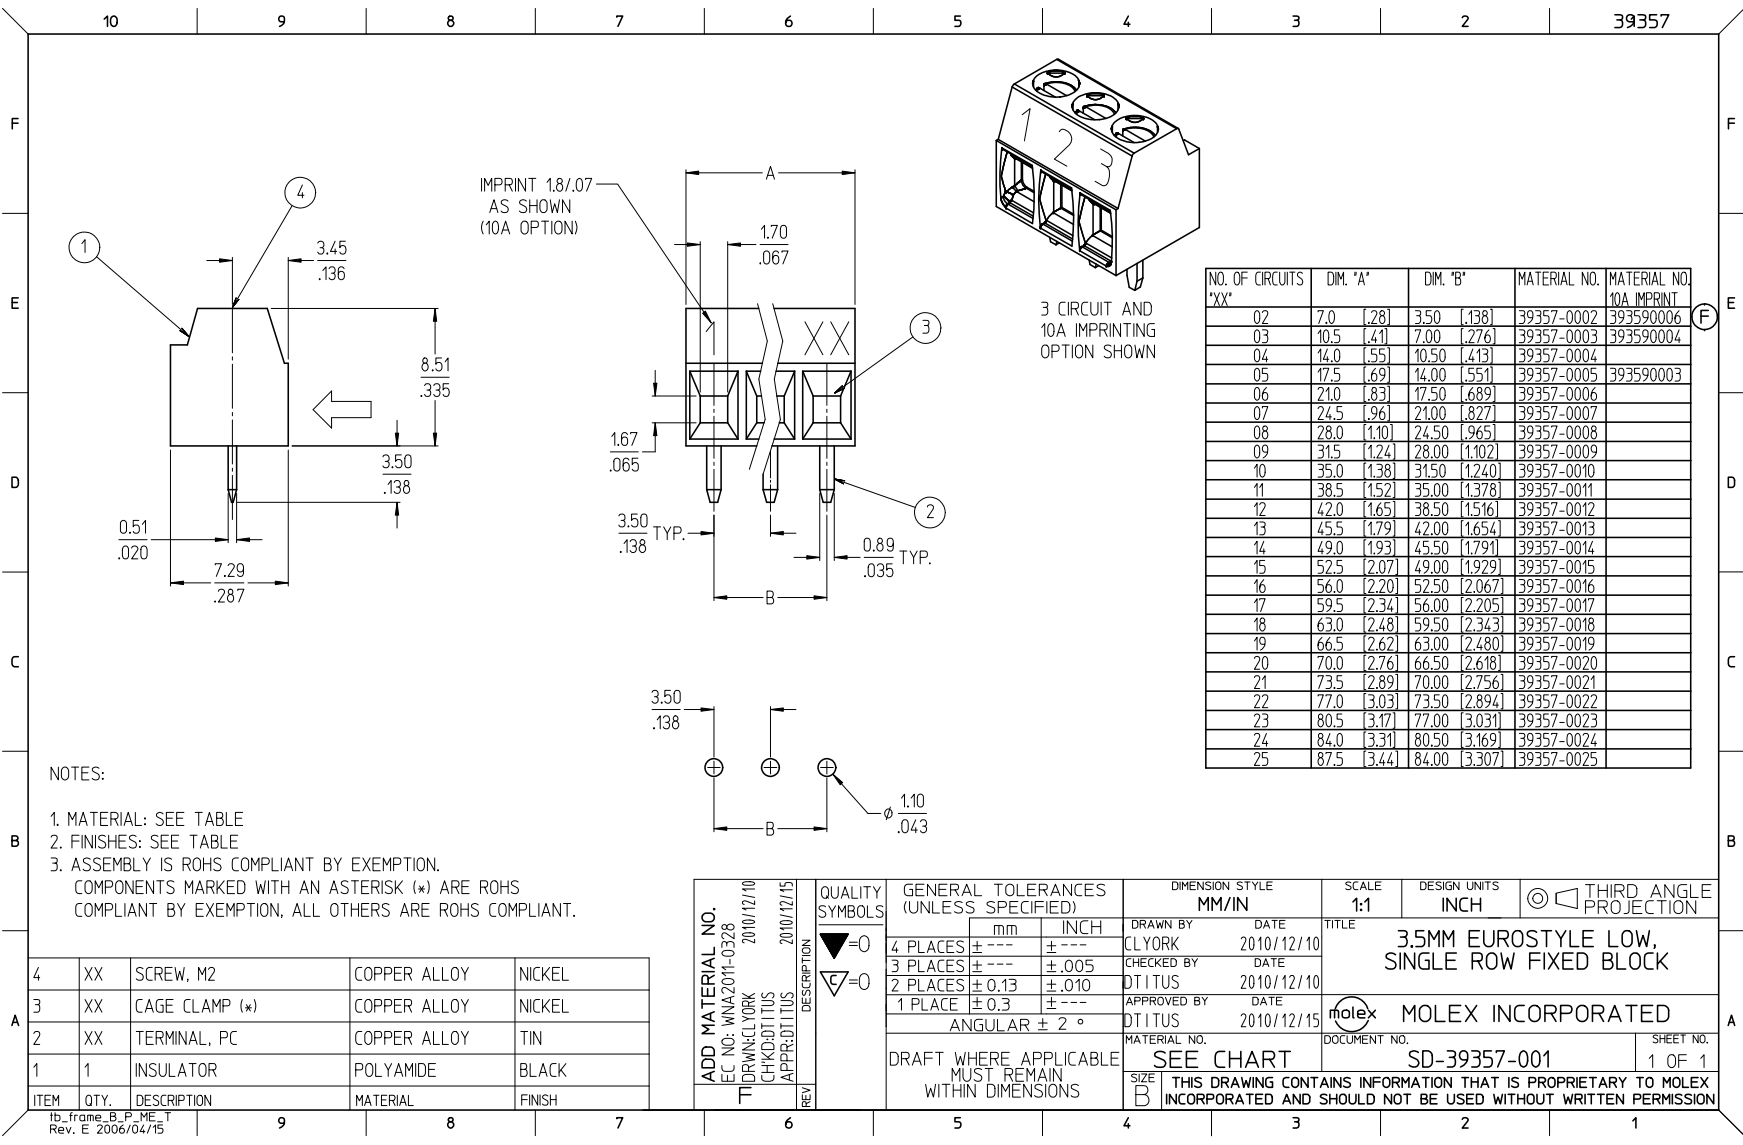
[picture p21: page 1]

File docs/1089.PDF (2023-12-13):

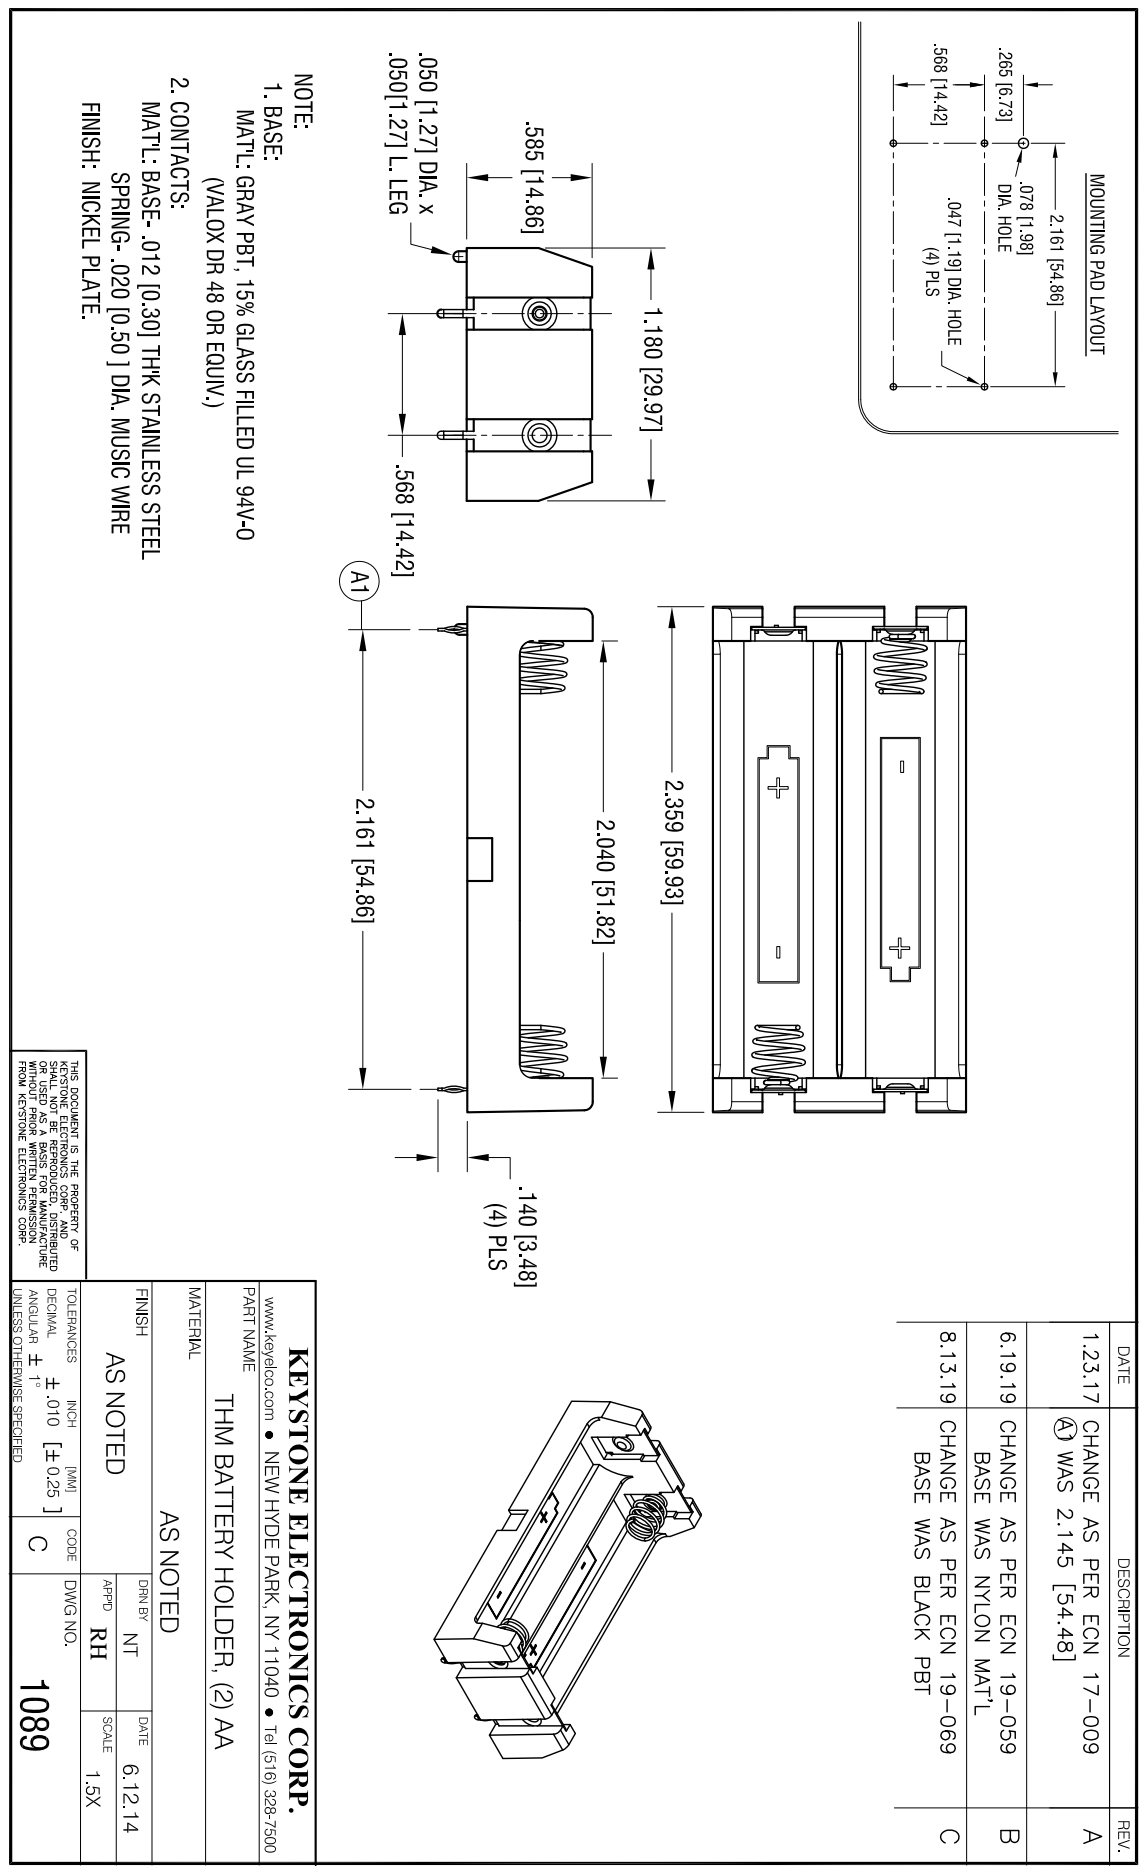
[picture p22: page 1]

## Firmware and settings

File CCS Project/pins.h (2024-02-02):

/*
 * pins.h
 *
 * Defines all of the pins we are using
 *
 *  Created on: Oct 15, 2022
 *      Author: josh
 */

#ifndef PINS_H_
#define PINS_H_


// --- RV3032 RTC

// RV3032 Event input pin is hardwired to ground to avoid having it float during battery changes (uses lots of power)

// Power the RV3032 on pin P1.2 which is pin number 26 on MSP430

#define RV3032_VCC_PREN P1REN
#define RV3032_VCC_PDIR P1DIR
#define RV3032_VCC_POUT P1OUT
#define RV3032_VCC_PIN  P1IN

#define RV3032_VCC_B (2)

// Ground the RV3032 on pin P1.3 which is pin number 23 on MSP430
// Having the RV30332 ground come from the MCU should give extra isolation since it runs though the MSP decoupling cap
// and this also makes sure their grounds are close together.

#define RV3032_GND_PREN P1REN
#define RV3032_GND_PDIR P1DIR
#define RV3032_GND_POUT P1OUT
#define RV3032_GND_PIN  P1IN

#define RV3032_GND_B (3)


// Connected to the RV3203 INT pin which is open collector on RV3032 side

#define RV3032_INT_PREN   P1REN
#define RV3032_INT_PDIR   P1DIR
#define RV3032_INT_POUT   P1OUT
#define RV3032_INT_PIN    P1IN
#define RV3032_INT_PIE    P1IE          // Interrupt enable
#define RV3032_INT_PIV    P1IV          // Interrupt vector (read this to get which pin caused interrupt, reading clears highest pending)
#define RV3032_INT_PIFG   P1IFG         // Interrupt flag (bit 1 for each pin that interrupted)
#define RV3032_INT_PIES   P1IES         // Interrupt Edge Select (0=low-to-high 1=high-to-low)

#define RV3032_INT_B (4)       // Bit


// Connected to the RV3203 CLKOUT pin
// This is the source of the vast, vast, vast majority of all of our wakes
// durring product lifetime, so it is on a dedicated interrupt vector
// so the ISR does not need to check the source/

#define RV3032_CLKOUT_PREN   P2REN
#define RV3032_CLKOUT_PDIR   P2DIR
#define RV3032_CLKOUT_POUT   P2OUT
#define RV3032_CLKOUT_PIN    P2IN
#define RV3032_CLKOUT_PIE    P2IE          // Interrupt enable
#define RV3032_CLKOUT_PIV    P2IV          // Interrupt vector (read this to get which pin caused interrupt, reading clears highest pending)
#define RV3032_CLKOUT_PIFG   P2IFG         // Interrupt flag (bit 1 for each pin that interrupted)
#define RV3032_CLKOUT_PIES   P2IES         // Interrupt Edge Select (0=low-to-high 1=high-to-low)
#define RV3032_CLKOUT_VECTOR PORT2_VECTOR  // ISR vector

#define RV3032_CLKOUT_B (0)       // Bit

// I2C data connection to RV3032 on pin P1.5 which is pin number 23 on MSP430

#define I2C_DTA_PREN P1REN
#define I2C_DTA_PDIR P1DIR
#define I2C_DTA_POUT P1OUT
#define I2C_DTA_PIN  P1IN
#define I2C_DTA_B (5)       // Bit

// I2C clock connection to RV3032 on pin P1.0 which is pin number 28 on MSP430

#define I2C_CLK_PREN P1REN
#define I2C_CLK_PDIR P1DIR
#define I2C_CLK_POUT P1OUT
#define I2C_CLK_PIN  P1IN

#define I2C_CLK_B (0)



// --- DEBUG PINS


// Debug out A on pin P1.7 which is pin number 21 on MSP430

#define DEBUGA_PREN P1REN
#define DEBUGA_PDIR P1DIR
#define DEBUGA_POUT P1OUT
#define DEBUGA_PIN  P1IN

#define DEBUGA_B (7)


// Debug out B on pin P8.3 which is pin number 19 on MSP430

#define DEBUGB_PREN P1REN
#define DEBUGB_PDIR P1DIR
#define DEBUGB_POUT P1OUT
#define DEBUGB_PIN  P1IN

#define DEBUGB_B (6)


// --- SOLENOIDS

#define S1_PREN P7REN
#define S1_PDIR P7DIR
#define S1_POUT P7OUT
#define S1_PIN  P7IN
#define S1_B (0)       // Bit

#define S2_PREN P7REN
#define S2_PDIR P7DIR
#define S2_POUT P7OUT
#define S2_PIN  P7IN
#define S2_B (1)       // Bit

#define S3_PREN P7REN
#define S3_PDIR P7DIR
#define S3_POUT P7OUT
#define S3_PIN  P7IN
#define S3_B (2)       // Bit

#define S4_PREN P7REN
#define S4_PDIR P7DIR
#define S4_POUT P7OUT
#define S4_PIN  P7IN
#define S4_B (3)       // Bit

#define S5_PREN P7REN
#define S5_PDIR P7DIR
#define S5_POUT P7OUT
#define S5_PIN  P7IN
#define S5_B (4)       // Bit

#define S6_PREN P7REN
#define S6_PDIR P7DIR
#define S6_POUT P7OUT
#define S6_PIN  P7IN
#define S6_B (5)       // Bit


// --- SWITCHES - Note these are on an interrupt enabled port

#define SWITCH_MOVE_PREN   P1REN
#define SWITCH_MOVE_PDIR   P1DIR
#define SWITCH_MOVE_POUT   P1OUT
#define SWITCH_MOVE_PIN    P1IN
#define SWITCH_MOVE_PIE    P1IE           // Interrupt enable
#define SWITCH_MOVE_PIV    P1IV           // Interrupt vector (read this to get which pin caused interrupt, reading clears highest pending)
#define SWITCH_MOVE_PIFG   P1IFG          // Interrupt flag (bit 1 for each pin that interrupted)
#define SWITCH_MOVE_PIES   P1IES          // Interrupt Edge Select (0=low-to-high 1=high-to-low)
#define SWITCH_MOVE_VECTOR PORT1_VECTOR   // ISR vector
#define SWITCH_MOVE_B (7)
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

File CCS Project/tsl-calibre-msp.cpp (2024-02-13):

#include <msp430.h>

#include "util.h"
#include "pins.h"
#include "i2c_master.h"

#include "error_codes.h"

#include "ram_isrs.h"

#include "tsl_asm.h"

#include "define_lcd_pinout.h"
#include "define_lcd_to_msp430_connections.h"
#include "define_msp430_lcd_device.h"
#include "define_lcd_font.h"

#include "lcd_display.h"
#include "lcd_display_exp.h"

#define RV_3032_I2C_ADDR (0b01010001)           // Datasheet 6.6

// RV3032 Registers

#define RV3032_HUNDS_REG 0x00    // Hundredths of seconds
#define RV3032_SECS_REG  0x01
#define RV3032_MINS_REG  0x02
#define RV3032_HOURS_REG 0x03
#define RV3032_DAYS_REG  0x05
#define RV3032_MONS_REG  0x06
#define RV3032_YEARS_REG 0x07

// Used to time how long ISRs take with an oscilloscope

/*
// DEBUG VERSIONS
#define DEBUG_PULSE_ON()     SBI( DEBUGA_POUT , DEBUGA_B )
#define DEBUG_PULSE_OFF()    CBI( DEBUGA_POUT , DEBUGA_B )
*/

// PRODUCTION VERSIONS
#define DEBUG_PULSE_ON()     {}
#define DEBUG_PULSE_OFF()    {}


// If this is defined, the LCD will use an optional TPS7A voltage regulator attached to the bias pin.
// If it is not defined, the we will configure the LCD to use the internal voltage reference.
// Using the TPS7A reduces LCD total power significantly (about 40%), at the cost of an extra part.
// Note that if a TPS7A is connected to pin 33 and the internal reference is enabled, it will waste lots of power even if the TPS7A is not enabled.
#define USE_TPS7A_LCD_BIAS




// Turn off power to RV3032 (also takes care of making the IO pin not float and disabling the inetrrupt)
void depower_rv3032() {

    CBI( RV3032_CLKOUT_PIE , RV3032_CLKOUT_B );     // Disable interrupt so we do not get a spurious one doing this stuff.

    // Make Vcc pin to RV3032 ground.
    CBI( RV3032_VCC_POUT , RV3032_VCC_B);

    // Now the CLKOUT pin is floating, so we will pull it
    SBI( RV3032_CLKOUT_PREN , RV3032_CLKOUT_B );    // Enable pull resistor (does not matter which way, just keep pin from floating to save power)

}

// Goes into LPM3.5 to save power since we can never wake from here.
// In LPMx.0 draws 1.38uA with the "First STart" message.
// In LPMx.5 draws 1.13uA with the "First STart" message.

// Clearing GIE does not prevent wakeup from LPMx.5 so all interrupts must have been individually disabled.
#pragma FUNC_NEVER_RETURNS
void sleepforeverandever(){

    // These lines enable the LPMx.5 modes
    PMMCTL0_H = PMMPW_H;                    // Open PMM Registers for write
    PMMCTL0_L |= PMMREGOFF_L;               // and set PMMREGOFF

    // Make sure no pending interrupts here or else they might wake us!
    __bis_SR_register(LPM3_bits);     // // Enter LPM4 and sleep forever and ever and ever (no interrupts enabled so we will never get woken up)

}

// Assumes all interrupts have been individually disabled.
#pragma FUNC_NEVER_RETURNS
void blinkforeverandever(){
    lcd_blinking_mode_all();
    sleepforeverandever();
}

// Assumes all interrupts have been individually disabled.
#pragma FUNC_NEVER_RETURNS
void error_mode( byte code ) {
    lcd_show_errorcode(code);
    blinkforeverandever();
}

void sleep_with_interrupts() {
    __bis_SR_register(LPM4_bits | GIE );                // Enter LPM4
    __no_operation();                                   // For debugger
}

// Does not enable interrupts on any pins

inline void initGPIO() {

    // Default pin init. We will also (possabibly duplicatively) init individual pins
    // TODO: use the full word-wide registers
    // Initialize all GPIO pins for low power OUTPUT + LOW
    P1DIR = 0xFF;P2DIR = 0xFF;P3DIR = 0xFF;P4DIR = 0xFF;
    P5DIR = 0xFF;P6DIR = 0xFF;P7DIR = 0xFF;P8DIR = 0xFF;
    // Configure all GPIO to Output Low
    P1OUT = 0x00;P2OUT = 0x00;P3OUT = 0x00;P4OUT = 0x00;
    P5OUT = 0x00;P6OUT = 0x00;P7OUT = 0x00;P8OUT = 0x00;

    // --- Solenoid MOSFETs off

    // Set Solenoid transistor pins to output off
    // Note that they are also pulled down by 100K ohm resistors so they do not float before we get here during reset
    CBI( S1_POUT , S1_B );
    CBI( S2_POUT , S2_B );
    CBI( S3_POUT , S3_B );
    CBI( S4_POUT , S4_B );
    CBI( S5_POUT , S5_B );
    CBI( S6_POUT , S6_B );

    SBI( S1_PDIR , S1_B );
    SBI( S2_PDIR , S2_B );
    SBI( S3_PDIR , S3_B );
    SBI( S4_PDIR , S4_B );
    SBI( S5_PDIR , S5_B );
    SBI( S6_PDIR , S6_B );


    // --- Optional TPS7A regulator external bias voltage source

    // TODO: Test power savings from regulator to see if it is worth the extra part.

    // Make the pins output. They will stay low if the TPS7A is not configured.
    // There is other code in initLCD that will turn on the internal bias generator if USE_TPS7A_LCD_BIAS is not defined.

    // Set all the pins to the TPS7A to out
    // This will ground them if the TPS7A is not enabled so they do not float.
    SBI( TSP_IN_PDIR , TSP_IN_B );          // Power in pin
    SBI( TSP_ENABLE_PDIR , TSP_ENABLE_B );  // Enable pin

    #ifdef USE_TPS7A_LCD_BIAS

        SBI( TSP_IN_POUT , TSP_IN_B );          // Power up TPS7A
        SBI( TSP_ENABLE_POUT , TSP_ENABLE_B );  // Enable TSP

    #endif

    // --- Debug pins

    // Debug pins
    SBI( DEBUGA_PDIR , DEBUGA_B );          // DEBUGA=Output. Currently used to time how long the ISR takes

    CBI( DEBUGB_PDIR , DEBUGB_B );          // DEBUGB=Input
    SBI( DEBUGB_POUT , DEBUGB_B );          // Pull up
    SBI( DEBUGB_PREN , DEBUGB_B );

    // --- RV3032

    // ~INT in from RV3032 is an open collector output.
    // We don't use this for now, so set to drive low to avoid any power leakage.

    SBI( RV3032_INT_PDIR , RV3032_INT_B ); // OUTPUT, default low

    // Note that we can leave the RV3032 EVI pin as is - tied LOW on the PCB so it does not float (we do not use it)
    // It is hard tied low so that it does not float during battery changes when the MCU will not be running

    // Power to RV3032

    CBI( RV3032_GND_POUT , RV3032_GND_B);
    SBI( RV3032_GND_PDIR , RV3032_GND_B);

    SBI( RV3032_VCC_PDIR , RV3032_VCC_B);
    SBI( RV3032_VCC_POUT , RV3032_VCC_B);

    // Now we need to setup interrupt on RTC CLKOUT pin to wake us on each rising edge (1Hz)

    CBI( RV3032_CLKOUT_PDIR , RV3032_CLKOUT_B );    // Set input
    CBI( RV3032_CLKOUT_PIES , RV3032_CLKOUT_B );    // Interrupt on rising edge (Driven by RV3032 CLKOUT pin which we program to run at 1Hz).

    /* RV3230 App Guide Section 4.21.1:
     *  the 1 Hz clock can be enabled
     *  on CLKOUT pin. The positive edge corresponds to the 1 Hz tick for the clock counter increment (except for
     *  the possible positive edge when the STOP bit is cleared).
     */

    // Note that we do not enable the CLKOUT interrupt until we enter RTL or TSL mode

    // --- Trigger

    // By default we set the trigger to drive low so it will not use power regardless if the pin is in or out.
    // When the trigger is out, the pin is shorted to ground.
    // We will switch it to pull-up later if we need to (because we have not launched yet).

    CBI( SWITCH_TRIGGER_POUT , SWITCH_TRIGGER_B );      // low
    SBI( SWITCH_TRIGGER_PDIR , SWITCH_TRIGGER_B );      // drive
    SBI( SWITCH_TRIGGER_PREN , SWITCH_TRIGGER_B );      // Set pull mode to UP when POUT is high and PDIR is low (no effect when pin is in OUTPUT mode)
    SBI( SWITCH_TRIGGER_PIES , SWITCH_TRIGGER_B );      // Interrupt on high-to-low transition (pin pulled up, switch connects to ground)

    // --- Buttons

    // By default we set the switches to drive low so it will not use power in case the button is stuck or shorted
    // We will switch it to pull-up later if we need to (because we have not launched yet).

    CBI( SWITCH_MOVE_POUT , SWITCH_MOVE_B );      // low
    SBI( SWITCH_MOVE_PDIR , SWITCH_MOVE_B );      // drive
    SBI( SWITCH_MOVE_PREN , SWITCH_MOVE_B );      // Set pull mode to UP when POUT is high and PDIR is low (no effect when pin is in OUTPUT mode)
    SBI( SWITCH_MOVE_PIES , SWITCH_MOVE_B );      // Interrupt on high-to-low transition (pin pulled up, button connects to ground)

    CBI( SWITCH_CHANGE_POUT , SWITCH_CHANGE_B );      // low
    SBI( SWITCH_CHANGE_PDIR , SWITCH_CHANGE_B );      // drive
    SBI( SWITCH_CHANGE_PREN , SWITCH_CHANGE_B );      // Set pull mode to UP when POUT is high and PDIR is low (no effect when pin is in OUTPUT mode)
    SBI( SWITCH_CHANGE_PIES , SWITCH_CHANGE_B );      // Interrupt on high-to-low transition (pin pulled up, button connects to ground)

    // Note that we do not enable the trigger pin interrupt here. It will get enabled when we
    // switch to ready-to-lanch mode when the trigger is inserted at the factory. The interrupt will then get
    // disabled again and the pull up will get disabled after the trigger is pulled since once that happens we
    // dont care about the trigger state anymore and we don't want to waste power with either the pull-up getting shorted to ground
    // if they leave the trigger out, or from unnecessary ISR calls if they put the trigger in and pull it out again (or if it breaks and bounces).

    // Disable IO on the LCD power pins
    SYSCFG2 |= LCDPCTL;

    // Disable the GPIO power-on default high-impedance mode
    // to activate the above configured port settings
    PM5CTL0 &= ~LOCKLPM5;

}

// Low voltage flag indicates that the RTC has been re-powered and potentially lost its data.

// Initialize RV3032 for the first time
// Clears the low voltage flag
// sets clkout to 1Hz
// Disables backup function
// Does not enable any interrupts

void rv3032_init() {

    // Give the RV3230 a chance to wake up before we start pounding it.
    // POR refresh time(1) At power up ~66ms
    // Also there is Tdeb which is the time it takes to recover from a backup switch over back to Vcc. It is unclear if this is 1ms or 1000ms so lets be safe.
    __delay_cycles(1100000);    // 1 sec +/-10% (we are running at 1Mhz)

    // Initialize our i2c pins as pull-up
    i2c_init();


    // Set all the registers we care about that can get reset by either power-on-reset or recover from backup
    //uint8_t clkout2_reg = 0b00000000;        // CLKOUT XTAL low freq mode, freq=32768Hz
    //uint8_t clkout2_reg = 0b00100000;        // CLKOUT XTAL low freq mode, freq=1024Hz
    uint8_t clkout2_reg = 0b01100000;        // CLKOUT XTAL low freq mode, freq=1Hz

    i2c_write( RV_3032_I2C_ADDR , 0xc3 , &clkout2_reg , 1 );

    // First control reg. Note that turning off backup switch-over seems to save ~0.1uA
    //uint8_t pmu_reg = 0b01010000;          // CLKOUT off, Direct backup switching mode, no charge pump, 0.6K OHM trickle resistor, trickle charge Vbackup to Vdd. Only predicted to use 50nA more than disabled.
    //uint8_t pmu_reg = 0b01100001;         // CLKOUT off, Level backup switching mode (2v) , no charge pump, 1K OHM trickle resistor, trickle charge Vbackup to Vdd. Predicted to use ~200nA more than disabled because of voltage monitor.
    //uint8_t pmu_reg = 0b01000000;         // CLKOUT off, Other disabled backup switching mode, no charge pump, trickle resistor off, trickle charge Vbackup to Vdd
    //uint8_t pmu_reg = 0b00011101;          // CLKOUT ON, Direct backup switching mode, no charge pump, 12K OHM trickle resistor, trickle charge Vbackup to Vdd.
    //uint8_t pmu_reg = 0b01000000;         // CLKOUT off, backup switchover disabled, no charge pump, 1K OHM trickle resistor, trickle charge off.
    uint8_t pmu_reg = 0b00000000;         // CLKOUT on, backup switchover disabled, no charge pump, 1K OHM trickle resistor, trickle charge off.


    // TODO: which is lower power, INT or CLKOUT?

    i2c_write( RV_3032_I2C_ADDR , 0xc0 , &pmu_reg , 1 );

    uint8_t control1_reg = 0b00000100;      // TE=0 so no periodic timer interrupt, EERD=1 to disable automatic EEPROM refresh (why would you want that?).
    i2c_write( RV_3032_I2C_ADDR , 0x10 , &control1_reg , 1 );

    i2c_shutdown();

}

// Clear the low voltage flags. These flags remember if the chip has seen a voltage low enough to make it loose time.

void rv3032_clear_LV_flags() {

    // Initialize our i2c pins as pull-up
    i2c_init();

    uint8_t status_reg=0x00;        // Set all flags to 0. Clears out the low voltage flag so if it is later set then we know that the chip lost power.
    i2c_write( RV_3032_I2C_ADDR , 0x0d , &status_reg , 1 );

    i2c_shutdown();

}


// Turn off the RTC to save some power. Only use this if you will NEVER need the RTC again (like if you are going into error mode).

void rv3032_shutdown() {

    i2c_init();

    uint8_t pmu_reg = 0b01000000;         // CLKOUT off, backup switchover disabled, no charge pump
    i2c_write( RV_3032_I2C_ADDR , 0xc0 , &pmu_reg , 1 );

    i2c_shutdown();

}


// This will reset the prescaller in the RTC so that the next tick will come 1000ms from now.

void rv3032_zero() {
    // Initialize our i2c pins as pull-up
    i2c_init();

    unsigned char zero =0;

    // Then zero out the RTC to start counting over again, starting now. Note that writing any value to the seconds register resets the sub-second counters to the beginning of the second.
    // "Writing to the Seconds register creates an immediate positive edge on the LOW signal on CLKOUT pin."
    i2c_write( RV_3032_I2C_ADDR , RV3032_SECS_REG  , &zero , sizeof( zero ) );

    i2c_shutdown();
}

// Shortcuts for setting the RAM vectors. Note we need the (void *) casts because the compiler won't let us make the vectors into `near __interrupt (* volatile vector)()` like it should.

#define SET_CLKOUT_VECTOR(x) do {RV3032_CLKOUT_VECTOR_RAM = (void *) x;} while (0)
#define SET_TRIGGER_VECTOR(x) do {TRIGGER_VECTOR_RAM = (void *) x;} while (0)

// Terminate after one day
bool testing_only_mode = false;

/*

// Called when trigger pin changes high to low, indicating the trigger has been pulled and we should start ticking.
// Note that this interrupt is only enabled when we enter ready-to-launch mode, and then it is disabled and also the pin in driven low
// when we then switch to time-since-lanuch mode, so this ISR can only get called in ready-to-lanuch mode.

__interrupt void trigger_isr(void) {

    DEBUG_PULSE_ON();

    // First we delay for about 1000 cycles / 1.1Mhz  = ~1ms
    // This will filter glitches since the pin will not still be low when we sample it after this delay. We want to be really sure!
    __delay_cycles( 1000 );

    // Then clear any interrupt flag that got us here.
    // Timing here is critical, we must clear the flag *before* we capture the pin state or we might miss a change
    CBI( TRIGGER_PIFG , TRIGGER_B );      // Clear any pending trigger pin interrupt flag

    // Grab the current trigger pin level
    unsigned triggerpin_level = TBI( TRIGGER_PIN , TRIGGER_B );

    // Now we can check to see if the trigger pin was still low
    // If it is not still low then we will return and this ISR will get called again if it goes low again or
    // if it went low between when we cleared the flag and when we sampled it (VERY small race window of only 1/8th of a microsecond, but hey we need to be perfect, it could be a once in a lifetime moment and we dont want to miss it!)

    if ( !triggerpin_level ) {      // trigger still pulled?

        // WE HAVE LIFTOFF!

        // Disable the trigger pin and drive low to save power and prevent any more interrupts from it
        // (if it stayed pulled up then it would draw power though the pull-up resistor whenever the pin was out)

        CBI( TRIGGER_POUT , TRIGGER_B );      // low
        SBI( TRIGGER_PDIR , TRIGGER_B );      // drive

        CBI( TRIGGER_PIFG , TRIGGER_B );      // Clear any pending interrupt (it could have gone high again since we sampled it). We already triggered so we don't care anymore.

        // Show all 0's on the LCD to quickly let the user know that we saw the pull
        lcd_show_zeros();

        // Do the actual launch, which will...
        // 1. Read the current RTC time and save it to FRAM
        // 2. Set the launchflag in FRAM so we will forevermore know that we did launch already.
        // 3. Reset the current RTC time to midnight 1/1/00.


        // Note that the time variables will already be initialized to zero from power up

        // We will get the next tick with a rising edge on CLKOUT in 1000ms. Make sure we return from this ISR before then.

        // Clear any pending RTC interrupt so we will not tick until the next pulse comes from RTC in 1000ms
        // There could be a race where an RTC interrupt comes in just after the trigger was pulled, in which case we would
        // have a pending interrupt that would get serviced immediately after we return from here, which would look ugly.
        // We could also see an interrupt if the CLKOUT signal was low when trigger pulled (50% likelihood) since it will go high on reset.

        CBI( RV3032_CLKOUT_PIFG , RV3032_CLKOUT_B );      // Clear any pending interrupt from CLKOUT

        // Start ticking from... now!
        // (We rely on the secs, mins, hours, and days_digits[] all having been init'ed to zeros.)


    }

    DEBUG_PULSE_OFF();

}

*/

/*

 1024hz RTL pattern readings with Energytrace over 5 mins
 FRPWR is cleared on each ISR call with the following line at the very top...
      BIC.W     #FRPWR,(GCCTL0) ;           // Disable FRAM. Writing to the register enables or disables the FRAM power supply.  0b = FRAM power supply disabled.
 It would be nice if we could permanently disable the FRAM, but does not seem possible on this chip because it is automatically enabled when exiting LPM.

 RAMFUNC  FRPWR  CLKOUT   I
 =======  =====  =====    =======
   Y        0     1kHz     0.354mA
   Y        0     1kHz     0.351mA
   Y        1     1kHz     0.385mA
   Y        1     1kHz     0.371mA
   Y        1     1kHz     0.372mA
   Y        1     1Hz      0.0021mA
   Y        1     1Hz      0.0021mA
   Y        0     1Hz      0.0021mA
   N        1     1Hz      0.0027mA
   N        1     1Hz      0.0027mA

*/





void solenoidOn( unsigned s ) {
    switch (s) {
    case 1:     SBI( S1_POUT , S1_B ); break;
    case 2:     SBI( S2_POUT , S2_B ); break;
    case 3:     SBI( S3_POUT , S3_B ); break;
    case 4:     SBI( S4_POUT , S4_B ); break;
    case 5:     SBI( S5_POUT , S5_B ); break;
    case 6:     SBI( S6_POUT , S6_B ); break;
    }

}

void solenoidOff( unsigned s ) {
    switch (s) {
    case 1:     CBI( S1_POUT , S1_B ); break;
    case 2:     CBI( S2_POUT , S2_B ); break;
    case 3:     CBI( S3_POUT , S3_B ); break;
    case 4:     CBI( S4_POUT , S4_B ); break;
    case 5:     CBI( S5_POUT , S5_B ); break;
    case 6:     CBI( S6_POUT , S6_B ); break;
    }

}


void fire_solenoid( unsigned s) {


    // First completely pull 1
    solenoidOn(s);
    __delay_cycles( 50000 );
    solenoidOff(s);

}


// Note that solenoid numbers match the PCB markings and range 1-6,
// where 1 is at 1 oclock and the go counter clockwise from there

void fire_solenoids() {


    // First completely pull 1
    fire_solenoid(1);
    fire_solenoid(2);
    fire_solenoid(1);
    fire_solenoid(2);

    // Next lets try to dither in 2
/*
    for( unsigned i = 0; i < 50 ; i ++ ) {

        solenoidOn(1);
        __delay_cycles( 100 );
        solenoidOff(1);

        solenoidOn(2);
        __delay_cycles( 900 );
        solenoidOff(2);


    }
*/
}

// open the pair of solenoids connected to a single lock slide.
// g can be 0,1, or 2.

// TODO: Potentially reduce the max current load by only giving one solenoid full power just long enough for it to pull, then PWM it while pulling the other one.
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
int main( void )
{

    WDTCTL = WDTPW | WDTHOLD | WDTSSEL__VLO;   // Give WD password, Stop watchdog timer, set WD source to VLO
                                               // The thinking is that maybe the watchdog will request the SMCLK even though it is stopped (this is implied by the datasheet flowchart)
                                               // Since we have to have VLO on for LCD anyway, mind as well point the WDT to it.
                                               // TODO: Test to see if it matters, although no reason to change it.

    // Disable the Voltage Supervisor (SVS=OFF) to save power since we don't care if the MSP430 goes low voltage
    // This code from LPM_4_5_2.c from TI resources
    PMMCTL0_H = PMMPW_H;                // Open PMM Registers for write
    PMMCTL0_L &= ~(SVSHE);              // Disable high-side SVS

    // Count the number of boot-ups since programming
    SYSCFG0 &= ~PFWP;                   // Program FRAM write enable
//    reset_counter_value++;
    SYSCFG0 |= PFWP;                    // Program FRAM write protected (not writable)


    // Init GPIO first to be safe.
    initGPIO();
    // Init LCD next so we can talk
    initLCD();

    // Power up display with a nice dash pattern
    lcd_show_dashes();

    //#warning stop here for now
    //while (1);

    // Initialize the RV3032 with proper clkout & backup settings.
    rv3032_init();

    //regulatorTest();

    start_setting_mode();
    sleep_with_interrupts();                    // Wait for interrupts to take over.

    // should never never get here.

    // Disable all interrupts since any interrupt will wake us from LPMx.5 and execute a reset, even if interrupts are disabled.
    // Since we never expect to get here, be safe and disable everything.

    CBI( RV3032_CLKOUT_PIE , RV3032_CLKOUT_B );     // Disable interrupt.
    CBI( RV3032_CLKOUT_PIFG , RV3032_CLKOUT_B );    // Clear any pending interrupt.

    // TODO: Make these error codes actually show something on 6 digit LCD
    error_mode( ERROR_MAIN_RETURN );                    // This would be very weird if we ever saw it.

}

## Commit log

2023-12-08 Initial clone from TSL-calibre-MSP repo. Stupid github will not let you fork your own repo. :/
    Projects are similar, so good starting point. Such a shame can not fork the TSL repo.
    Cloned from here...
    https://github.com/bigjosh/TSL-calibre-MSP/commit/74d69b6a5a9fec6171ba1a7cd56f8c9285138fdd
    [62-217D.STEP, BOM.csv, Ceramic_Capacitor_0603_h32mil (1).step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]
2023-12-13 In progress, but good stopping point.
    Schematic done except for replicating the solenoid blocks. PCB gross layout looking good.
    [BOM.csv, CT10-XXXX-G1-A.stp]
2023-12-13 I think fully laid out, just needs routing
    [6 DIGIT LCD v2.step, 82548PLCC-2_package_3D.stp, TS04-66-43-BK-160-SMT.stp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]
2023-12-27 Added digit chache builder code, but does not work.
    [tsl-calibre-msp.cpp]
2023-12-28 RTC working at 1Hz, LCD shows 6 digit counter with blinking dot.
2023-12-30 Update README.md with TPS7A power savings tests
2023-12-30 Swap the names of switches CHANGE and MOVE in the schematic and pins.h to match what ended up on the PCB legend.
    [pins.h]
2023-12-30 Fixed pin assignment of TSP ENABLE pin to match PCB.
    Wow, that was a hard bug to find since often the pin would float and and everything would work, but then sometimes... not.
    [pins.h]
2023-12-30 Button debounce working sweetly. Harder than it looks!
    Pushing either button will increment a counter on the LCD. The counter in the middle increments on every interrupt so you can see all the extra ones in the background that we do not see as presses.
2023-12-31 Basic blinking to show selected digit durring set mode working.
    Hardware blinking for lower power than normal display!
2023-12-31 Swap trigger and CLK_OUT pins so clock can be on dedicated ISR
    Now all the user inputs (buttons + lock trigger) are on a shared vector.
    [pins.h]
2023-12-31 Solenoids S1 and S2 working. Need to make sure we can keep both in at the same time.
2024-01-03 Clean up PCB layout
    Added a secondary Vcc line from the battery straight to the MCU and isolated MCU from the high current lines.
    Moved decoupling caps nearer to MCU and TPS pins.
    Moved a bunch of signals to the top layer.
2024-01-15 Before rollback to check old PCB Vcc traces
2024-01-15 Add 100 ohm resistor to Vcc to make low pass filter
    The voltage drop when the solenoids turn on ended up being too fast and the MCU was browning out.
    [BOM.csv]
2024-01-15 Added Vcc resistor to PCB
2024-01-18 Shift LCD placement up 2.5mm on PCB as per CW
2024-01-19 Update PCB for terminal block connections to solenoids
    [393570002.stp, Ceramic_Capacitor_0603.step, sot23-5.step]
2024-01-20 PCB cleaned up and ready to order.
2024-01-30 ISR driven countdown display works but not power optimized and no FRAM backup yet
2024-02-01 Countdown timer functionality running. Uses ~1.35uA straight C++ no ASM.
    Can't do any ASM optimization until we are sure this is the right UI.
    Still need to add in the backup counter function, but that is only an additional instruction per minute.
2024-02-02 Setting and triggering UI implemented and works
    Uses ~1.35uA between button presses.
2024-02-02 UI fully implemented. Just need to add the solenoid opening code!
    ...and power optimize the countdown mode stuffs.
2024-02-03 Functionally complete
    Rotate which pair of solenoids gets activated first on opening.
    Normalize all times when setting so, say, 49 hours becomes 2 days + 1 hour.
2024-02-06 Hide ugly gate traces on PCB. Closes #17
2024-02-06 Cleanup PCB
2024-02-08 Clean up PCB
    Actual terminal block pads got lost somewhere. now they are back.
2024-02-13 Power optimiation.
    Use hardware LCD blanking to show the blank page in the countdown. This is very power efficient because (1) we only need to change a single bit to show the blank screen rather than writing all of the segments to be blank, and (2) we can now *always* keep the HHMMSS page rendered in the LCDMEM bank so we only ever need to write the digits that actually change. I think this update code is now pretty damn close to being algorithmically optimal! The only way to make it more efficient now is to avoid the crappy compiler and implement in ASM.
    [tsl-calibre-msp.cpp]
